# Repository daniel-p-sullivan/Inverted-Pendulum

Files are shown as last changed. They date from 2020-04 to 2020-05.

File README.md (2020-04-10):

# Inverted-Pendulum
## An inverted pendulum project for learning about control theory.

### email:  daniel.p.sullivan@utexas.edu

I will continue to update this page with more information as my project progresses.

Please feel free to reach out with any comments/questions/suggestions.

#TODO
- [ ] Swing up problem
  - [ ] Offline trajectory optimization
  - [ ] Energy based controller
- [ ] Integral action, LQI Problem
- [ ] Lyapunov stability

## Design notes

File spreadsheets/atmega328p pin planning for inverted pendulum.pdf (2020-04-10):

Hook up all encoders, button to 5V and ground.

328P port configurations

use this for interrupts | PORTD for reading encoders
PCMKS2 | 7 | 6 | 5 | 4 | 3 | 2 | 1 | 0
| PCINT23 | PCINT22 | PCINT21 | PCINT20 | PCINT19 | PCINT18 | PCINT17 | PCINT16
portd | PD7 | PD6 | PD5 | PD4 | PD3 | PD2 | PD1 | PD0
arduino pins | digital pin 7 | digital pin 6 | digital pin 5 | digital pin 4 | digital pin 3 | digital pin 2 | digital pin 1 | digital pin 0
pendulum component | | | rotary encoder | rotary encoder | rotary encoder | rotary encoder
cart or pend? | | | cart | cart | pendulum | pendulum
wire colors | | | green | white | white | green

PORTB for PWM
PORTB | 7 | 6 | 5 | 4 | 3 | 2 | 1 | 0
arduino pins | crystal | crystal | digital 13 | digital 12 | digital 11 | digital 10 | digital 9 | digital 8
pendulum component | | | | | | | PWM | state transition
| | | | | | | | button

PORTC for motor direction control
PORTC | 7 | 6 | 5 | 4 | 3 | 2 | 1 | 0
arduino pin | ? | reset | ai5 | ai4 | ai3 | ai2 | ai1 | ai0
pendulum component | | | | | | | motor control | motor control
l298n connection | | | | | | | IN1 | IN2

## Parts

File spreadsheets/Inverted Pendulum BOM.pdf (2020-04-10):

# BOM for Inverted Pendulum

Item | QTY | Part | Link
1 | 1 Arduino Uno | https://www.amazon.com/Arduino-A000066-ARDUINO-UNO-R3/dp/B008GRTSV6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
2 | 2 Rotary Encoder | https://www.amazon.com/gp/product/B00UTIFCVA/ref=ppx_yo_dt_b_asin_title_o07_s00?ie=UTF8&psc=1
3 | 1 12V DC Motor | https://www.amazon.com/gp/product/B072R5G5GR/ref=ppx_yo_dt_b_asin_title_o01_s00?ie=UTF8&psc=1
4 | 1 Motor Driver | https://www.amazon.com/gp/product/B014KMHSW6/ref=ppx_yo_dt_b_asin_title_o09_s00?ie=UTF8&psc=1
5 | 1 Linear Rail | https://www.amazon.com/gp/product/B07GBQ8GTY/ref=ppx_yo_dt_b_asin_title_o06_s00?ie=UTF8&psc=1
6 | 4 10mm standoffs | https://www.digikey.com/product-detail/en/keystone-electronics/24337/36-24337-ND/1532138
| 7 ~3ft | 3GT timing belt | https://openbuildspartstore.com/3gt-gt2-3m-timing-belt-by-the-foot/
8 | 2 Belt Clamps | https://openbuildspartstore.com/belt-clamp-crimp-style/
9 | 1 M3 screws/hex | https://www.amazon.com/gp/product/B072FKMYMF/ref=ppx_yo_dt_b_asin_title_o05_s00?ie=UTF8&psc=1
10 | 2 Timing Pulley | https://openbuildspartstore.com/3gt-gt2-3m-timing-pulley-20-tooth-250-bore-9mm-belt/

If you don't have a DC Power Supply w/ 12V capability I'd recommend getting one of these and filling it with AA batteries:
11 | 1 12V Battery Case | https://www.amazon.com/gp/product/B00VE7HBMS/ref=ppx_yo_dt_b_asin_title_o00_s00?ie=UTF8&psc=1

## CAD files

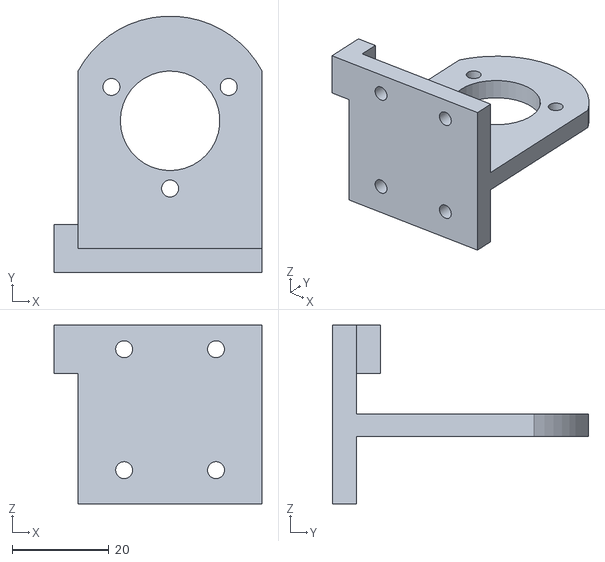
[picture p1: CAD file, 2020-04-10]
stl files/prototype_encoder_mount.STL
43.0 x 53.0 x 37.0

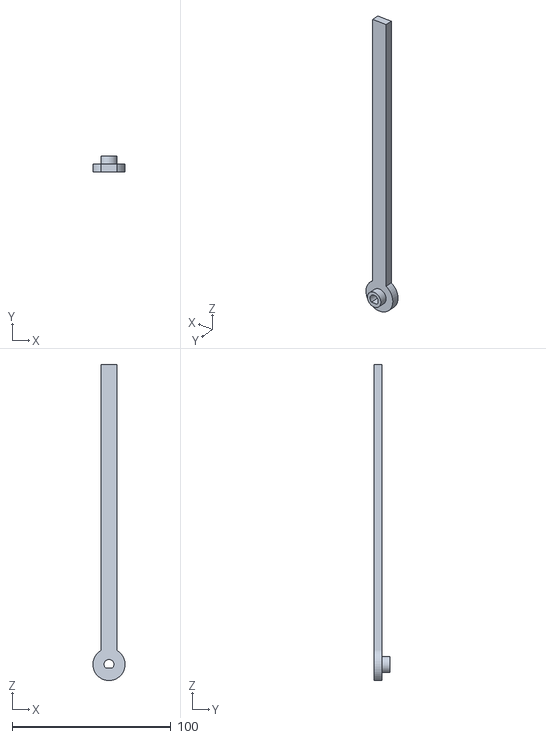
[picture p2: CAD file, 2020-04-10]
stl files/pendulum.STL
20.3 x 10.2 x 198.9

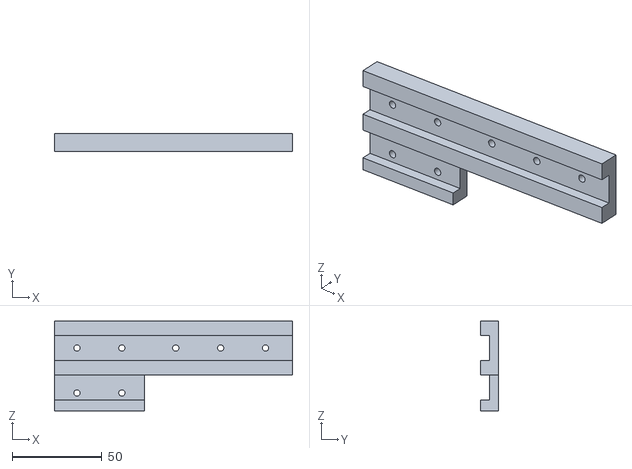
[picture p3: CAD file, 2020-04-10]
stl files/motor_rail_mount.STL
132.5 x 10.0 x 50.0

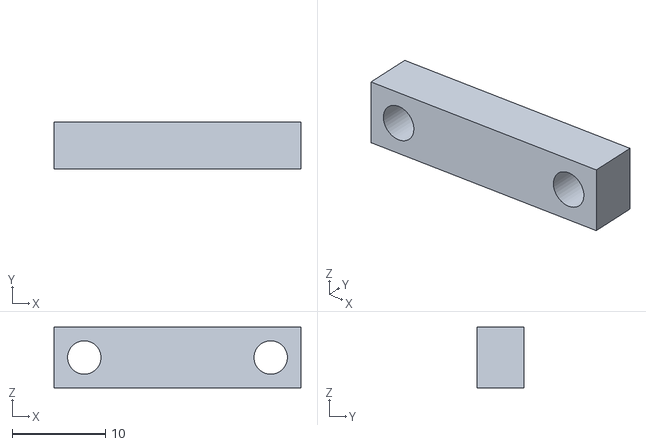
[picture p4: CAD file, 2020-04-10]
stl files/spacer.STL
26.5 x 5.08 x 6.50

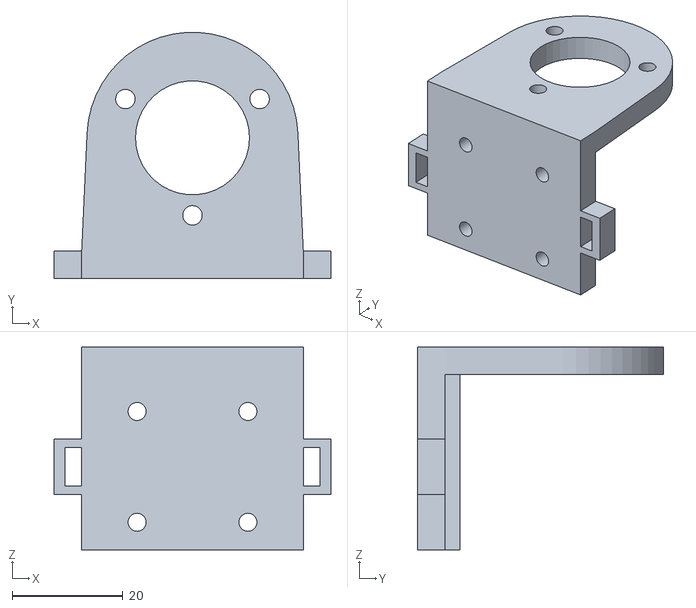
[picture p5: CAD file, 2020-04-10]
stl files/linear_rail_encoder_mount.STL
50.0 x 44.4 x 36.6

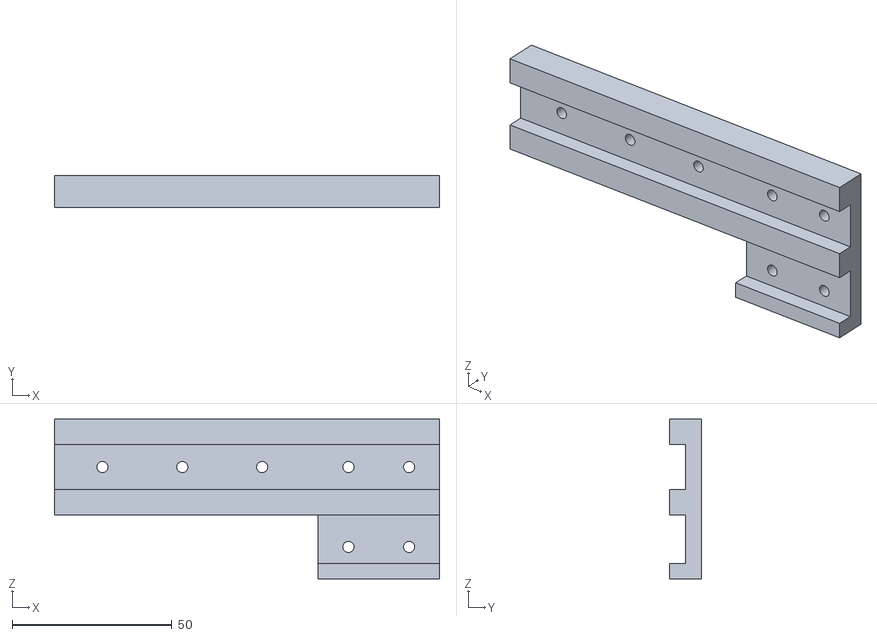
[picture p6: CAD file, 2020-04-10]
stl files/encoder_rail_mount.STL
120.5 x 10.0 x 50.0

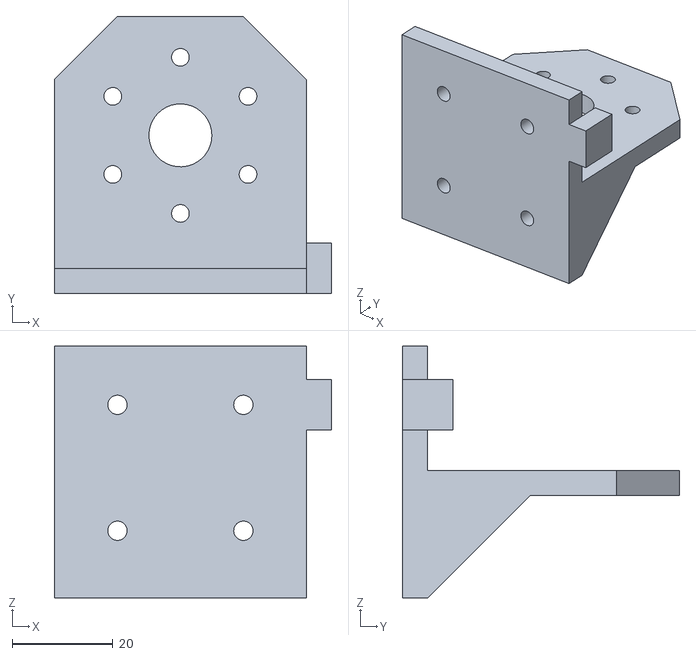
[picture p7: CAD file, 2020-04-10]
stl files/prototype_motor_mount.STL
55.0 x 55.0 x 50.0

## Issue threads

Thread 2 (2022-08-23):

PID controller and future work

eleftheria15, 2022-08-23:
Hi Daniel,

Thanks for this project. I replicated your setup, and it really served me well as a base for my project extension.

Instead of Arduino Uno, I've used an ARM-based processor, namely Raspberry Pi 3 Model B

I plan to switch between PID and LQR (eventually MPC) inside the event loop during run-time after a certain pre-specified periodicity.

However, it seems that PID is not able to work properly (in my setup) as the only angle (not position) is taken into account.

Can you let me know whether you've tested the PID controller in your setup?

Also, are there any updates regarding the swing-up problem and MPC optimization?

daniel-p-sullivan, 2022-08-23:
Hi Aleksandar,

Glad you like the project!
I still need to work on mine more - I started a quadcopter flight control
project and haven’t returned to this one.

As far as I remember the PID controller is able to work properly.
How is yours malfunctioning?
Maybe the gains are tuned improperly.
I will test this in my setup soon and let you know.

In regards to your comment on: “ only angle (not position) is taken into
account.”
Could you expand on this?
In my setup (and in the current GitHub code) the position of the cart is
measured/estimated via a rotary encoder input.

Best regards,

Daniel Sullivan

On Tue, Aug 23, 2022 at 8:54 AM Aleksandar Matovic ***@***.***>
wrote:

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

eleftheria15, 2022-08-23:
Yes, I meant that position is left uncontrollable and that you can probably design PID in such a way that it's taking position into account, as I assume this would provide better stability. This is something that I was thinking it's making stability issues.

However, if you say it works in your setup, I will go back to Arduino Uno and double-check with modified gains.

Also, the gains are different in my Raspberry Pi setup, as it is much more powerful, so you need a sleep time after each iteration. I'll make the pull request to upload the RPi code here.

I assume the video in the repo was made using LQR as a control technique. It would be great if you could confirm that PID is working in your setup so that I can be sure that hardware is the problem in mine.

Bests,
Aleksandar

daniel-p-sullivan, 2023-03-25:
Hi Aleksandar
Sorry for taking awhile to get back to you.
PID is working in my setup - the pendulum is balanced upright, but cannot maintain a position on the track.
LQR does maintain the cart position and pendulum angle though.

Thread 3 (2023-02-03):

State transition button

Xeroxsch, 2023-02-03:
Could you please explain the working of the state transition button? I mean why do you need it.
I am following your code for mine. Also could you please tell me how to convert cpr into ppr for encoder? One of my encoder has lower resolution than the other ...so will i be able to do the control with your code?

daniel-p-sullivan, 2023-03-25:
Hi
Yeah the state transition button is just connected to the breadboard.
When my code starts, the motor is not actuating at all, and the setpoint is not set.
Pressing the state transition button does 2 things in my code:
1. The current rotary encoder measurement is saved in the setpoint var that the system will target.  So when I'm setting up the pendulum, I manually balance it upright before pressing this button.
2. The control system will start actively working; control algos will run and the motor will be driven with their outputs.

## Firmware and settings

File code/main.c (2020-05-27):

/*
 * main.c for Inverted Pendulum project
 *
 * Created: 9/11/2015
 * Author : Daniel Sullivan
 */ 

#define F_CPU 16000000L // Specify oscillator frequency
#include <avr/io.h>
#include <util/delay.h>
#include <avr/pgmspace.h>
#include <avr/sfr_defs.h>
#include <avr/interrupt.h>
#include <stdio.h>
#include <stdlib.h>
#include <stdbool.h>
#include <string.h>
#include "control_functions.h"
#include "hardware.h"

#define derivative_sample_size 5//have to do this b/c C is dumb
#define message_sample_size 10000
#define sample_size 50 //sample size for data acquisition

//baud rate
unsigned int baud = 9600;

//loop counter
static long loop_count = 0;

//variables for the rotary encoder(s) count and angle
volatile long rot_pendulum = 0;
volatile long rot_cart = 0;
double angle = 0;
double angular_velocity;
double position = 0;
double velocity = 0;
double previous_angle;
double previous_position;

//moving average arrays
double angular_velocity_ma[derivative_sample_size];
double velocity_ma[derivative_sample_size];

//moving average helper variables
double oldest_angular_velocity;
double oldest_velocity;

//time variables
double current_time_millis;
double previous_time_millis;
double current_time;
double previous_time;
double dt;
double dt_millis;

//timer handling variables
volatile unsigned long timer0_overflow_count = 0;
long double millis_per_timer0_tick = 0.064;
double millis_per_overflow = 16.32;
static uint8_t timer0_byte = 0;

//other conversion factors
const float angle_conversion_factor_degrees = 0.15;		//rotary encoders have 600 pulses per rotation
const float angle_conversion_factor_rads = 0.00261799;	//rotary encoders have 600 pulses per rotation
const float position_conversion_factor = 0.000025; //converts pulses to radians, then [m] using Rpulley

//setpoint variables that are set during debounce()
double x_desired = 0.0;
double xdot_desired = 0.0;
double theta_desired = 3.14159265;
double thetadot_desired = 0;

//error variables
double x_error = 0;
double xdot_error = 0;
double theta_error = 0;
double thetadot_error = 0;

//state machine controlling variable
int state = 0;

//stores output from motor driver to eventually store into PWM compare register
static uint16_t compare_register_set;

//message to be sent
char message[40];
char outstr[9];

//for sending floats
char* tempsign;
float tempval;
float tempfrac;
int tempint1;
int tempint2;

int sample_index = 0;
int count_until_sample = 50; //take sample every 50 runs of the control loop
double t_array[sample_size];
long rot_pend_array[sample_size];
double thetadot_array[sample_size];
long rot_cart_array[sample_size];
double velocity_array[sample_size];
int input_array[sample_size];
	
void USART_Init(unsigned int ubrr){
	/*Set baud rate */
	UBRR0H = (unsigned char)(ubrr>>8);
	UBRR0L = (unsigned char)ubrr;
	/* Enable receiver and transmitter */
	UCSR0B = (1<<RXEN0)|(1<<TXEN0);
	/* Set frame format: 8data, 2stop bit */
	UCSR0C = (1<<USBS0)|(3<<UCSZ00);
}

void USART_Transmit(unsigned char data){
	/* Wait for empty transmit buffer */
	while (!(UCSR0A & (1<<UDRE0)));
	/* Put data into buffer, sends the data */
	UDR0 = data;
}

unsigned char USART_Receive(void)
{
	/* Wait for data to be received */
	while (!(UCSR0A & (1<<RXC0)));
	/* Get and return received data from buffer */
	return UDR0;
}

ISR(PCINT2_vect){
	
	static const int8_t rot_states[] = {0, -1, 1, 0, 1, 0, 0, -1, -1, 0, 0, 1, 0, 1, -1, 0};
	static uint8_t AB[2] = {0x03, 0x03};  //for storing old and new values of pins
	uint8_t t = PIND;                      //read Port B
	t = (t >> 2) & 0b00001111;								//used to keep dig pin 0/1 open for TX/RX in futue
	
	//check for rotary state change
	AB[0] <<= 2;       //save previous state (by bit shifting it left)
	AB[0] |= t & 0x03; //add the new state to the 2 LSB of AB (by making this the 2 LSB)
	rot_pendulum += rot_states[AB[0] & 0x0f]; //increment or decrement the rotation
	
	AB[1] <<= 2;		//save previous state
	AB[1] |= (t >> 2) & 0x03; //shift t to the right two (move 2nd r.e. inputs to the LSB) 
	rot_cart += rot_states[AB[1] & 0x0f]; //increment or decrement
}

ISR(TIMER0_OVF_vect){
	
	timer0_overflow_count++;

}

long double millis(){
	//read the low byte before the high byte
	timer0_byte = TCNT0;
	return (long double)timer0_overflow_count * millis_per_overflow + timer0_byte * millis_per_timer0_tick;
}

void transmit_data(char* data){
	//for(int i = 0; data[i] != '\0'; i++){
	while(*data!='\0'){
		USART_Transmit(*data++);
	}
}

static inline void debounce(void){
	//Taken from some stackoverflow thread, forgot to get link
	static uint8_t count = 0;
	static uint8_t button_state = 0;
	uint8_t current_state = PINB & _BV(PB0);
	
	if(current_state != button_state){ //If the current state is different than the old state
		
		count++;					  //count number of times there is a difference
		
		if(count >= 4){				//if state is different > 4 times in a row
			button_state = current_state;	//set the state
			
			if(button_state == 1){			//if the button is now on
				state++;					//increment the "state" variable (will be used for state machine transition of overall system)
				if(state == 1){ //initial conditions for state1
					
					theta_desired = rot_pendulum * angle_conversion_factor_rads;
					x_desired = rot_cart * position_conversion_factor;
				}
				else if(state == 2){
					//initial conditions for state 2
				}
				
			}
			count = 0;
		}
	}
}

static inline void moving_average_derivative_calculation(){
	//moving average for derivative calculations
	oldest_angular_velocity = angular_velocity_ma[loop_count % derivative_sample_size];
	oldest_velocity = velocity_ma[loop_count % derivative_sample_size];
	angular_velocity_ma[loop_count % derivative_sample_size] = (angle - previous_angle) / dt;
	velocity_ma[loop_count % derivative_sample_size] = (position - previous_position) / dt;
	angular_velocity += ((angular_velocity_ma[loop_count % derivative_sample_size] - oldest_angular_velocity) / derivative_sample_size);
	velocity += ((velocity_ma[loop_count % derivative_sample_size] - oldest_velocity) / derivative_sample_size);
}

static inline void get_time_information(){
	//get time information
	current_time_millis = millis();
	current_time = current_time_millis * 0.001;
	dt = current_time - previous_time;
}

static inline void calculate_error(){
	//calculate errors
	x_error = position - x_desired;
	xdot_error = velocity - xdot_desired;
	theta_error = angle - theta_desired;
	thetadot_error = angular_velocity - thetadot_desired;
}

static inline void save_previous_states(){
	previous_position = position;
	previous_angle = angle;
	previous_time = current_time;
}

static inline void take_sample(){
	//only take sample every count_until_sample times
	if(loop_count % count_until_sample == 0){
		t_array[sample_index] = current_time;
		rot_cart_array[sample_index] = angle;
		thetadot_array[sample_index] = angular_velocity;
		rot_pend_array[sample_index] = position;
		velocity_array[sample_index] = velocity;
		input_array[sample_index] = compare_register_set;
		sample_index++;
	}
}

int main(void)
{
	//-------------SETUP---------------
	
	//Commented out this line as STATE 2 is currently commented out and data is not being sent back to the PC	
	//USART_Init(103);
	
	rotary_encoders_setup();
	motor_setup();
	timer_setup();
	
	//ENABLE GLOBAL INTERRUPTS
	sei();
	
	//-------------END SETUP-------------
    while(1)
    {
		//debounce the state transition button
		debounce();
		
		//reset the loop count
		loop_count = 0;
		
		while(state == 1 && sample_index < sample_size){
			
			//continue to debounce the state transition button
			debounce();
			
			//measurement estimates
			angle = (double)rot_pendulum * angle_conversion_factor_rads;
			position = (double)rot_cart * position_conversion_factor;
			
			get_time_information();
			
			moving_average_derivative_calculation();
			
			save_previous_states();
			
			calculate_error();
					
			//CONTROLLERS
				
			//P Controller
			//compare_register_set = motor_feedback_control(P(&angle));
				
			//PI Controller
			//compare_register_set = motor_feedback_control(PI(&angle, &dt));
				
			//LQR Controller
			compare_register_set = motor_feedback_control(LQR(&x_error, &xdot_error, &theta_error, &thetadot_error));
			OCR1A = compare_register_set;
			
			//commented out this line as currently data is not being sent back to the PC
			//take_sample();
			
			loop_count++;
		}
		//reset the loop count
		loop_count = 0;
		
		//reset the sample index
		sample_index = 0;
		while(state == 2){
			
			//STATE 2 is commented out as USART data sendback is currently poor
			
			//STATE 2:  SEND BACK DATA
			
			//debounce the state transition button
			//debounce();
			
			/*for(int i = 0; i < sample_size; i++){

				dtostrf(t_array[i], 9, 4, outstr);
				sprintf(message, "t:%s", outstr);
				transmit_data(message);
				
				dtostrf(thetadot_array[i], 9, 4, outstr);
				sprintf(message, "th:%ldtd:%s", rot_pend_array[i], outstr);
				transmit_data(message);
				
				dtostrf(velocity_array[i], 9, 4, outstr);
				sprintf(message, "x:%ldv:%su:%d", rot_cart_array[i], outstr, input_array[i]);
				transmit_data(message);
			}*/
			
			//once serial comms is done, move to next state
			state = 3;
		}
		loop_count++;
		
    }
}

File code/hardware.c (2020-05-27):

#include <avr/io.h>
#include <avr/pgmspace.h>
#include <stdlib.h>
#include "hardware.h"

//motor feedback variable
static double calculated_motor_feedback = 0;

//minimum allowable motor feedback
//This variable to be adjusted for the controller to overcome the friction
//TODO:  Calibrate this variable by increasing the PWM steadily until the cart moves?
static int minimum_motor_feedback = 0;

//for converting volt output of control calculation to PWM
//1023 / 12 [V] = 85.25
//Therefore, multiply this constant by the calculated voltage from the controller to scale the PWM correctly.
static const float pwm_conversion_factor = 85.25;

int motor_feedback_control(double* cmf){
	
	calculated_motor_feedback = *cmf * pwm_conversion_factor;   //cmf comes in in units of [V], multiply by
	//the pwm_conversion_factor to put it in units of PWM
	//set plant limits to PWM signal
	if(calculated_motor_feedback < minimum_motor_feedback && calculated_motor_feedback > 0){
		
		calculated_motor_feedback = minimum_motor_feedback;
		PORTC = 0b00000000 | _BV(PC0); //turn on PH0, turn off PH1
		
		}else if(calculated_motor_feedback > -minimum_motor_feedback && calculated_motor_feedback < 0){
		
		calculated_motor_feedback = -minimum_motor_feedback;
		PORTC = 0b00000000 | _BV(PC1);
		
		}else if(calculated_motor_feedback > 1023){
		
		calculated_motor_feedback = 1023;
		PORTC = 0b00000000 | _BV(PC0);
		
		}else if (calculated_motor_feedback < -1023){
		
		calculated_motor_feedback = -1023;
		PORTC = 0b00000000 | _BV(PC1);
		
		}else if (calculated_motor_feedback == 0){
		
		PORTC = 0b00000000;							//turn off PH0 and PH1
		
	}
	
	return abs(calculated_motor_feedback);		//set the compare register
}

void rotary_encoders_setup(){
	//Set up PORTD to accept the rotary encoder data
	PCICR |= _BV(PCIE2);  //turn on interrupt
	PCMSK2 |= _BV(PCINT21) | _BV(PCINT20) | _BV(PCINT19) | _BV(PCINT18); // enable pins on interrupt
	DDRD = 0b11000000;                   //all pins on Port B are inputs except for PD7/6
	PORTD = 0b00111100;                  //pullups for portD0, portD1, portD2, portD3
	PIND = 0b11000000;					 //release the brakes
}

void motor_setup(){
	//Set up PWM
	TCCR1A |= _BV(COM1A1) | _BV(WGM11) | _BV(WGM10); //set the COM1A1 pin to 1 for non-inverting mode, and the WGM0x pins to 1
	TCCR1B |= _BV(CS10);  /*don't set the force compare bits, _BV(CS12) if you want prescaling
							*WGM02 bit, select the clock with [(-101)1024 prescaler] [(-001) no prescaler)]
							*(use the prescaler for lower frequency PWM)*/
	
	OCR1A = 0x03ff;			//10-bit compare register, initially set at maximum
	DDRB = 0b0010010;		//pin 9 (PB1) is PWM, output, PB4 is status LED (red) control
	
	//Motor direction control on PORTC
	DDRC = 0b00000011;
}

void timer_setup(){
	PRR &= _BV(PRTIM2); 		//makes sure the PRTIM2 bit is off, timer1 used for PWM and timer0 used for millis()
	TCCR0B |= _BV(CS02) | _BV(CS00);	//1024bit prescaler
	//clock prescaler select (1024 prescaler used => 1 increment = 0.000064 [s] = 0.064 [ms]
}

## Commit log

2020-04-10 Create .stl files
2020-04-10 upload into correct folder
    [encoder_rail_mount.STL, linear_rail_encoder_mount.STL, motor_rail_mount.STL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]
2020-05-27 seperated some code into modules, updated main.c
    Added hardware and control functions modules. The hardware module contains functions for interfacing with rotary encoders, the timer, and the control of the DC motor. The control function module cont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
